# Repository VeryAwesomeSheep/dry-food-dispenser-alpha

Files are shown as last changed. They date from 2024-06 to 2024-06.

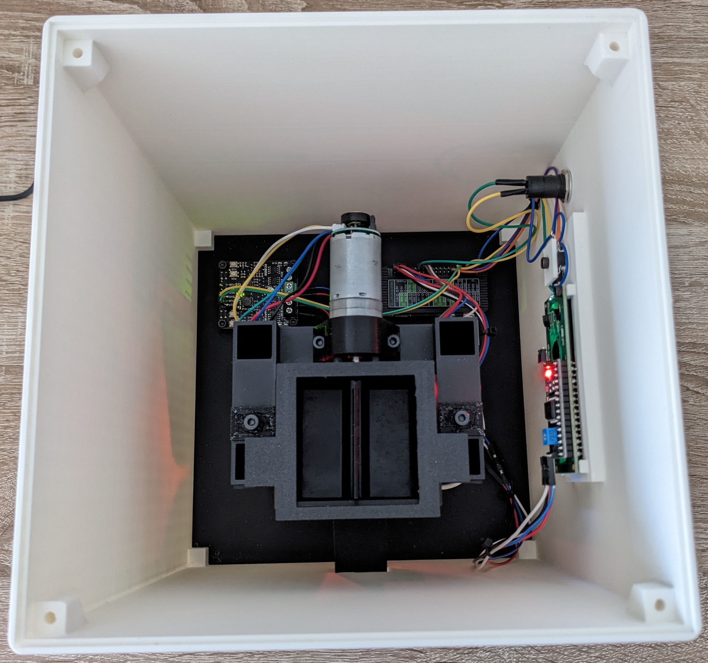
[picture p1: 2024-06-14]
Models/Pictures/inside.jpg

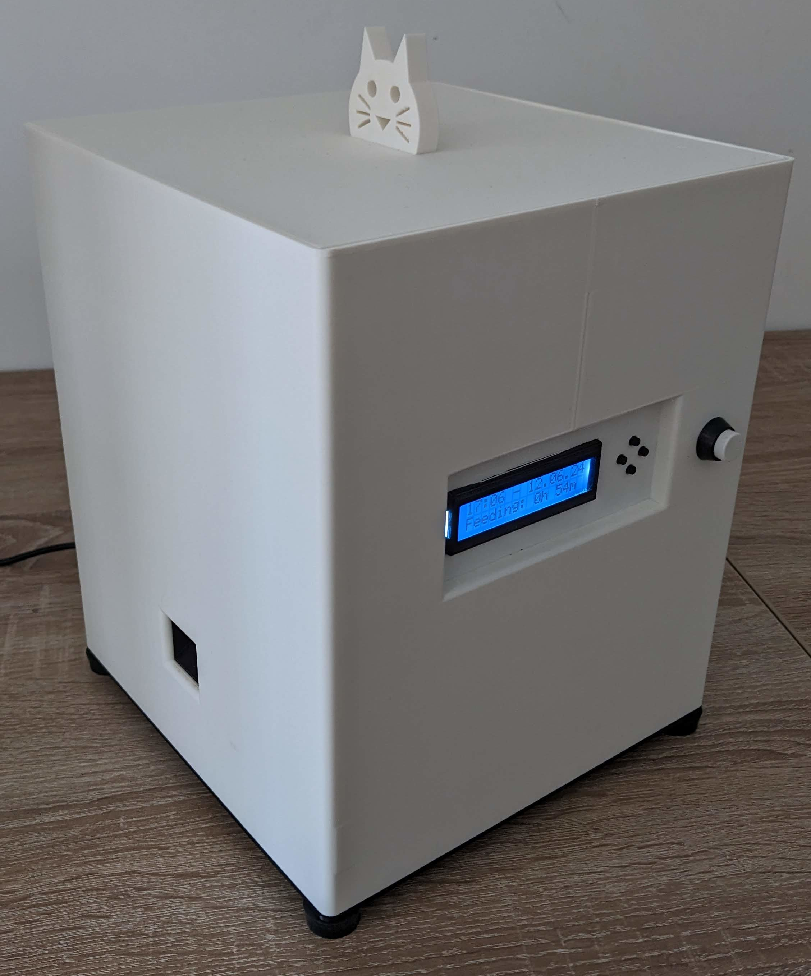
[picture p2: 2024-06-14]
Models/Pictures/front.jpg

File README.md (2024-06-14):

# dry-food-dispenser-alpha
Dry food dispenser for small pets. This was the project for my bachelor thesis. It's an alpha version that I plan on redesigning from the ground up in my spare time as I have some new, possibly better, ideas. All files are here, but I don't recommend building this version yourself.<br>

Project is based on Raspberry Pi Zero 2 W and is powered by a brushed DC motor. Communicaton with user is done via a simple 16x2 LCD display and 5 buttons in a pretty intuitive way. In 99% of cases button up is to go up or increase the value, button down is to go down or decrease the value, button left is to go back or cancel and button right is to go in or confirm. The fifth button called "feed" is used to give the pet a treat and can release a single portion of food when pressed by the user.<br>

Funcionalities of the system are:
- Dispensing food on schedule, fully configured by the user including the time of the day and the amount of portions of food. Limited to 10 feeding times per day, as it seemed more than enough, but it can be adjusted in the code if needed.
- Dispensing food on demand, by pressing the "feed" button.
- Configuring the amount of food per portion, by changing the feeding wheel and then setting the currently used wheel in the user menu.

<p align="center">
<center><image src="Models/Pictures/front.jpg" height="400"></center>
</p>

The dispenser is a fully closed system and it doesn't need any app or internet connection to work, but it's advised to connect the RPi to the internet once at boot to get the time and date for correct working of the scheduler.<br>

Whole system is written in C and it's GPIO functionality relies on [WiringPi](https://github.com/WiringPi/WiringPi) library. Just like the physical design, the code is also planned to be improved, especially the LCD handler as it's hard to read at times and some fragmentation is needed.<br>

The dispenser is powered by a 5V 4A power supply and the motor is controlled by Cytron MDD3A driver which is powered via step-up converter that bumps up the voltage to 6V for the motor. The motor is a 6V LP with 75:1 gearbox with and encoder providing 0.67Nm of torque.<br>

<p align="center">
<image src="Models/Pictures/schematic.png" height="550"></center>
</p>

All other parts are 3D printed and the idea behind them is to be easily mountable and demountable to allow for easy cleaning.

### BOM list
- 1x Raspberry Pi Zero 2 W
- 1x Cytron MDD3A motor driver
- 1x Pololu 2286 motor
- 1x 3-35V to 5-40V 5A step-up converter
- 1x 5V 4A DC power supply
- 1x 16x2 LCD display
- 1x LCD I2C adapter
- 4x Tact Switch TACT-67N
- 1x 12mm push button
- 1x DC-022b power socket
- 1x USB Micro B cabel
- 0.5mm² and 1.5mm² wires
- PLA filament
- PETG filament
- 12x M3x4 screw
- 3x M3x6 screw
- 6x M4x10 screw (+4 optional)
- 1x WaveShare Raspberry Pi Zero/Zero 2 W Heatsink
- 4x rubber feet

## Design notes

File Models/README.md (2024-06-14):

# Real life photos
### Front:
<center><image src="Pictures/front.jpg" height="400"></center>

### Back:
<center><image src="Pictures/back.jpg" height="400"></center>

### Inside:
<center><image src="Pictures/inside.jpg" height="400"></center>

### Inside with food compartment inserted:
<center><image src="Pictures/insideWithFoodCompartment.jpg" height="400"></center>

<br>

# Models:
### Base plate:
<center><image src="Pictures/base.jpg" height="400"></center>

### Cover:
<center><image src="Pictures/cover.jpg" height="400"></center>

### Top cap:
<center><image src="Pictures/topCap.jpg" height="200"></center>

### Food compartment:
<center><image src="Pictures/foodCompartment.jpg" height="400"></center>

### Feeding wheel:
<center><image src="Pictures/millWheel.jpg" height="400"></center>

### Feeding whele cover:
<center><image src="Pictures/wheelCover.jpg" height="400"></center>

### Feeding wheel cover plate:
<center><image src="Pictures/wheelCoverPlate.jpg" height="400"></center>

### Motor holder:
<center><image src="Pictures/motorHolderWithMotor.jpg" height="200"></center>

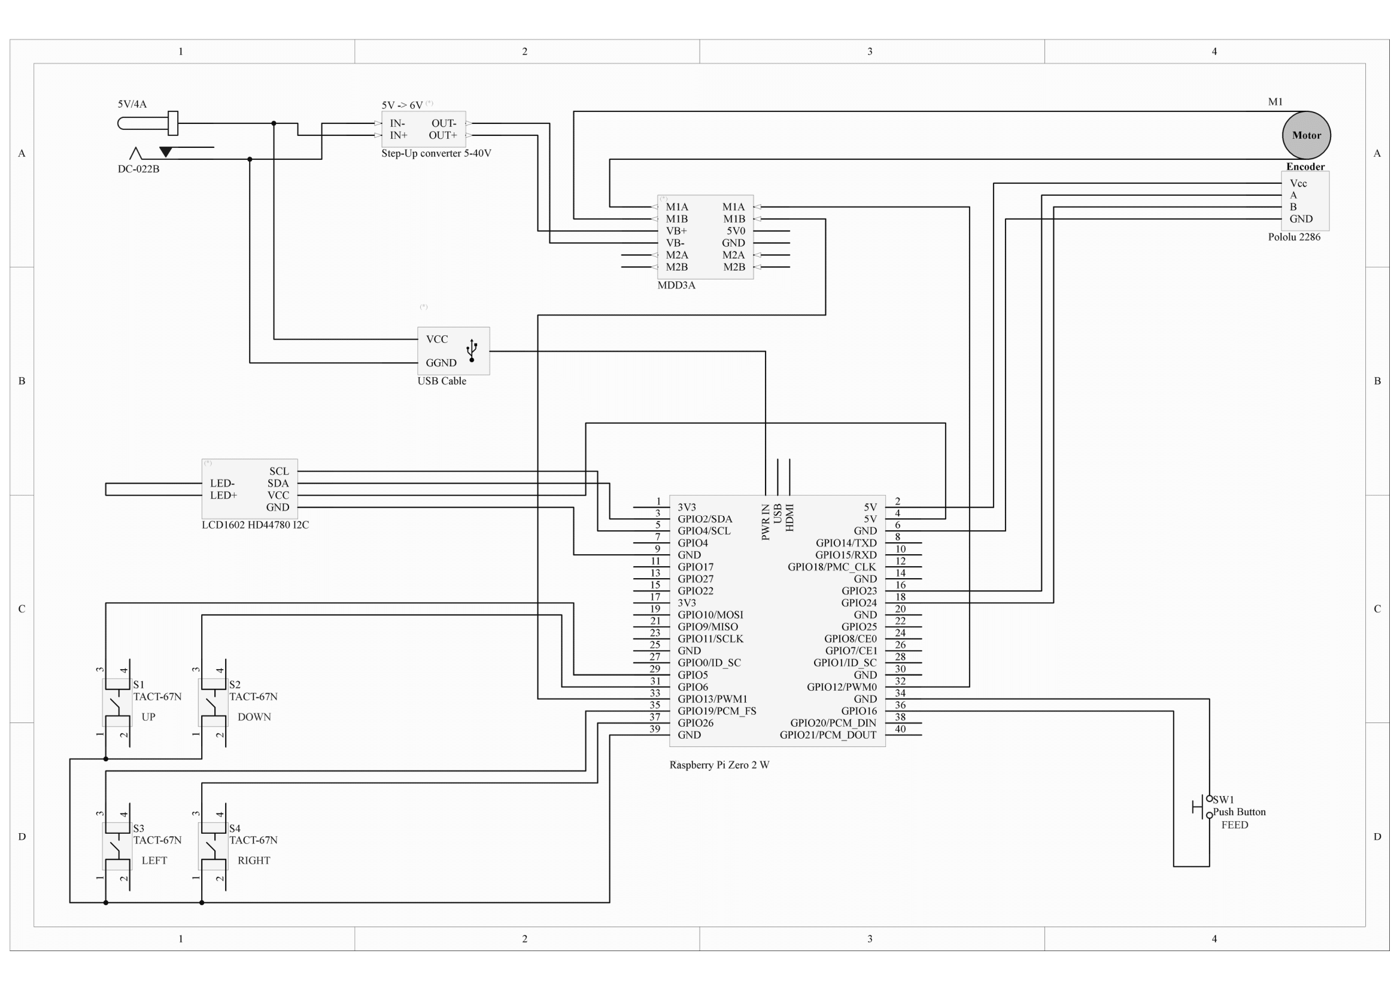
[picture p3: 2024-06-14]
Models/Pictures/schematic.png

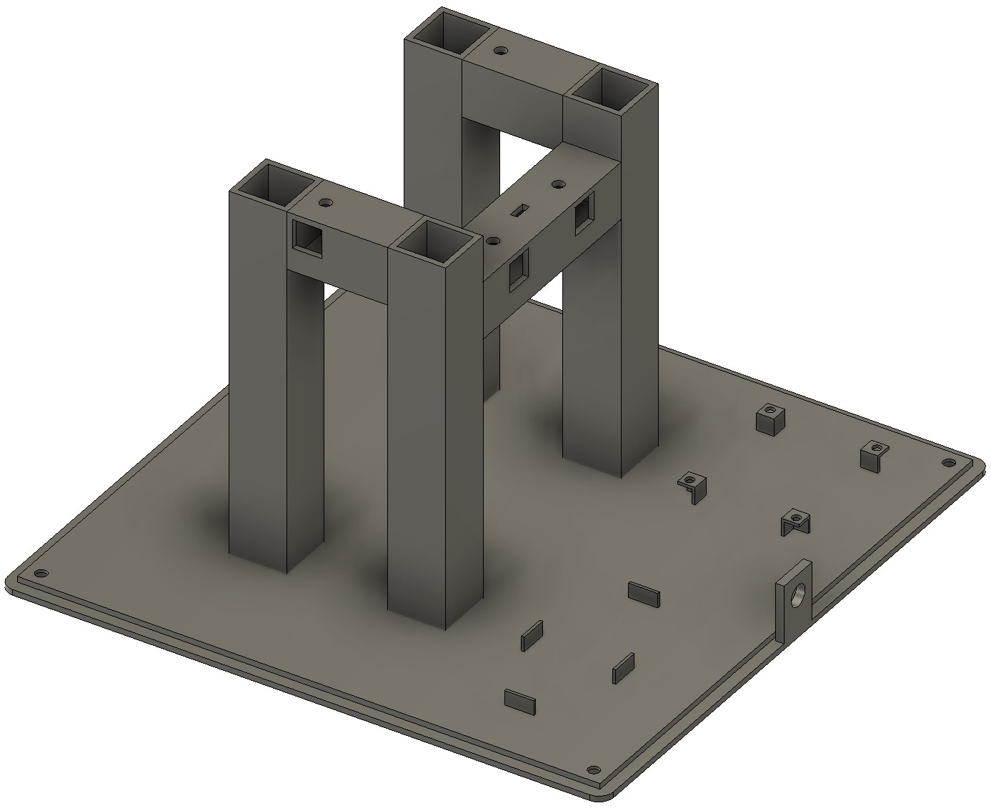
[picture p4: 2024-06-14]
Models/Pictures/base.jpg

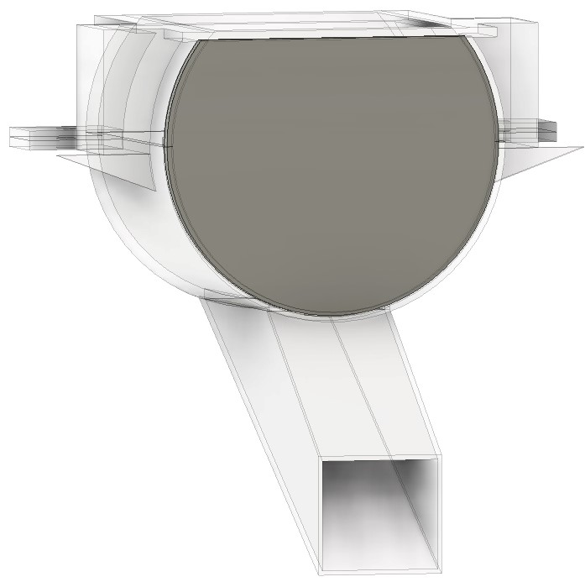
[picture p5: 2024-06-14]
Models/Pictures/wheelCoverPlate.jpg

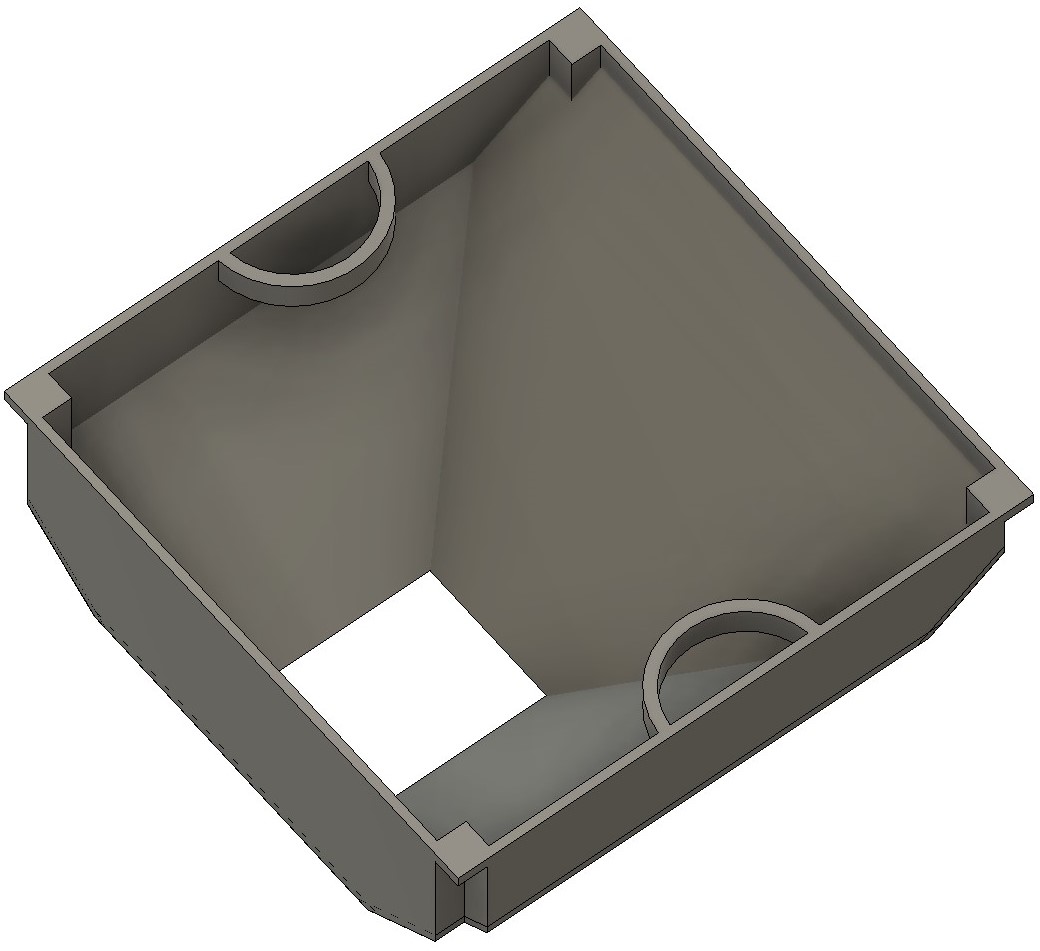
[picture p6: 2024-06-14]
Models/Pictures/foodCompartment.jpg

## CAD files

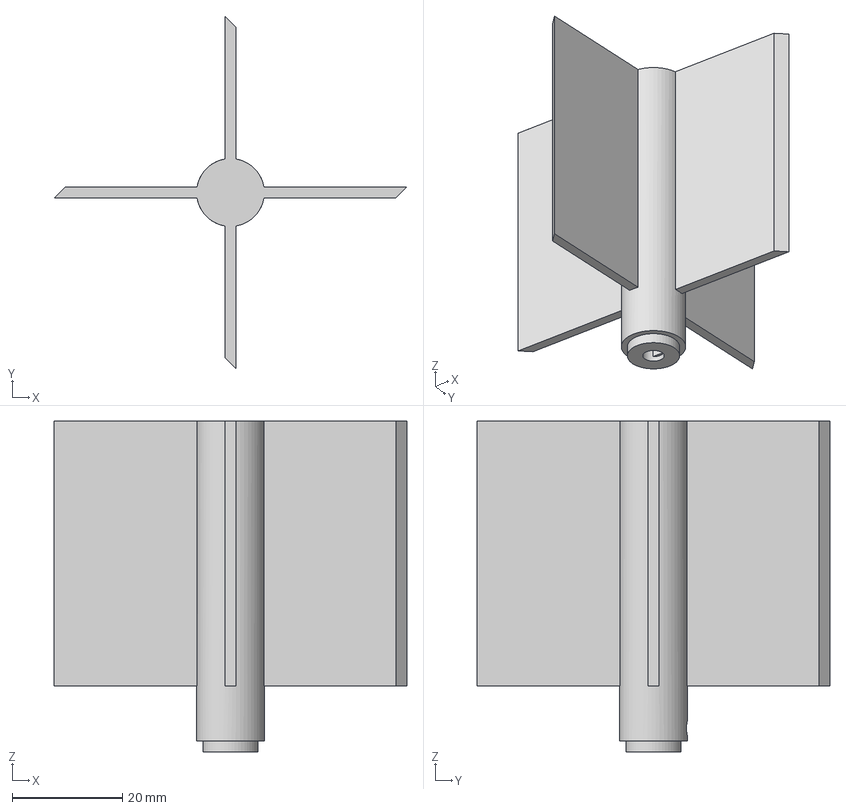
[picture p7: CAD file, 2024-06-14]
Models/Parts/MillWheel.step
64.0 x 64.0 x 60.0 mm

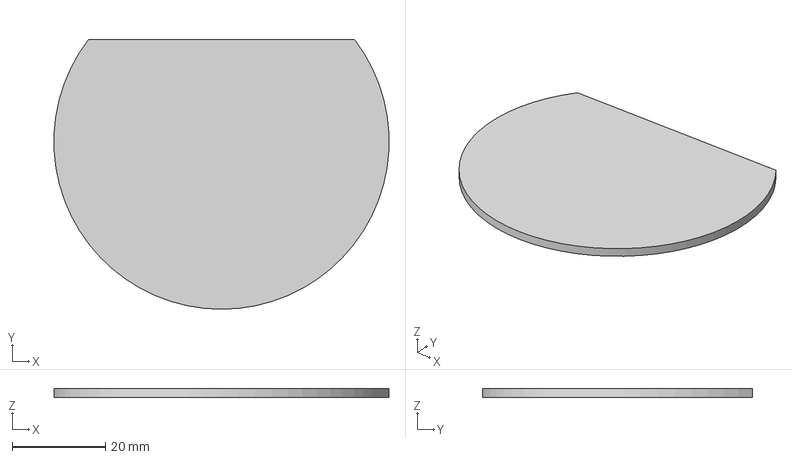
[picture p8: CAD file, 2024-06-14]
Models/Parts/MillWheelClosingPlate.step
71.7 x 57.7 x 2.00 mm

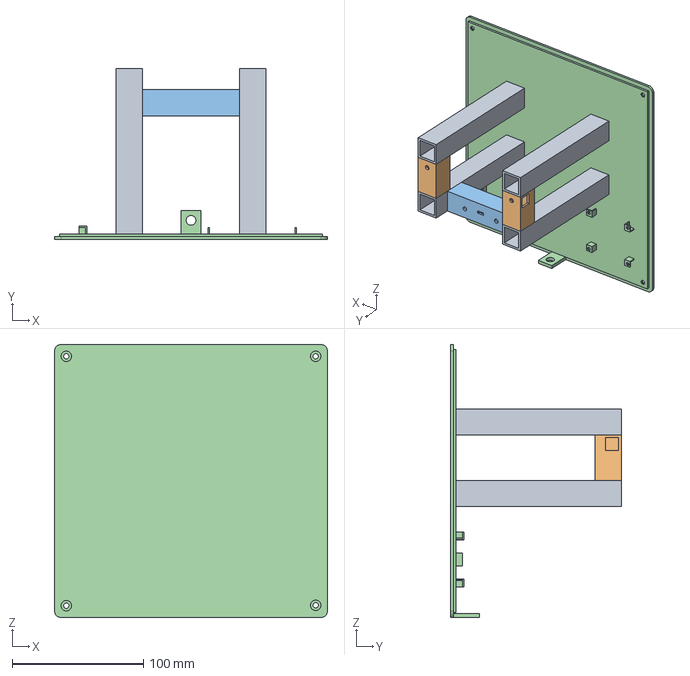
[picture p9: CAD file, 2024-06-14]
Models/Parts/BasePlate.step
208.0 x 130.0 x 208.0 mm

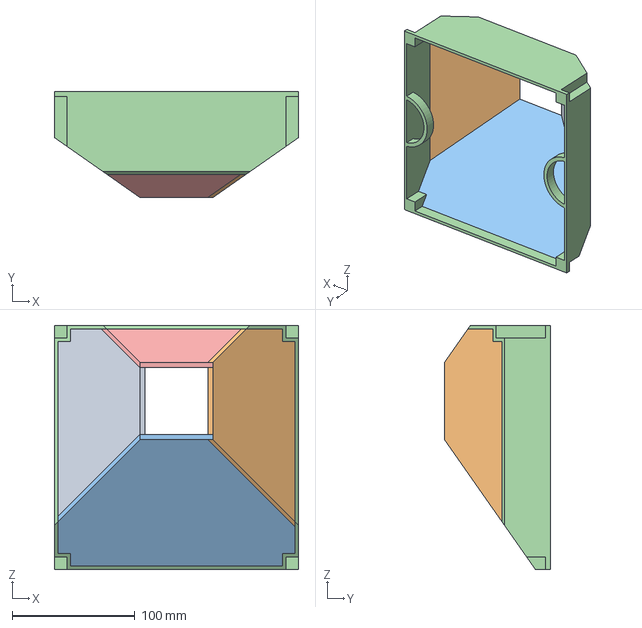
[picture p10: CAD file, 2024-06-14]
Models/Parts/FoodCompartment.step
198.5 x 86.2 x 198.5 mm

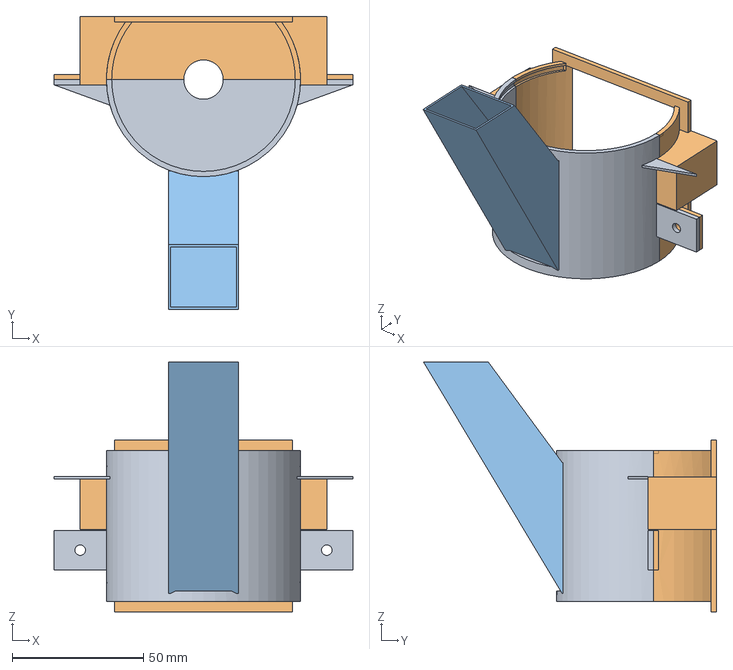
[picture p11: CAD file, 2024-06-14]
Models/Parts/MillWheelCover.step
114.0 x 111.6 x 95.1 mm

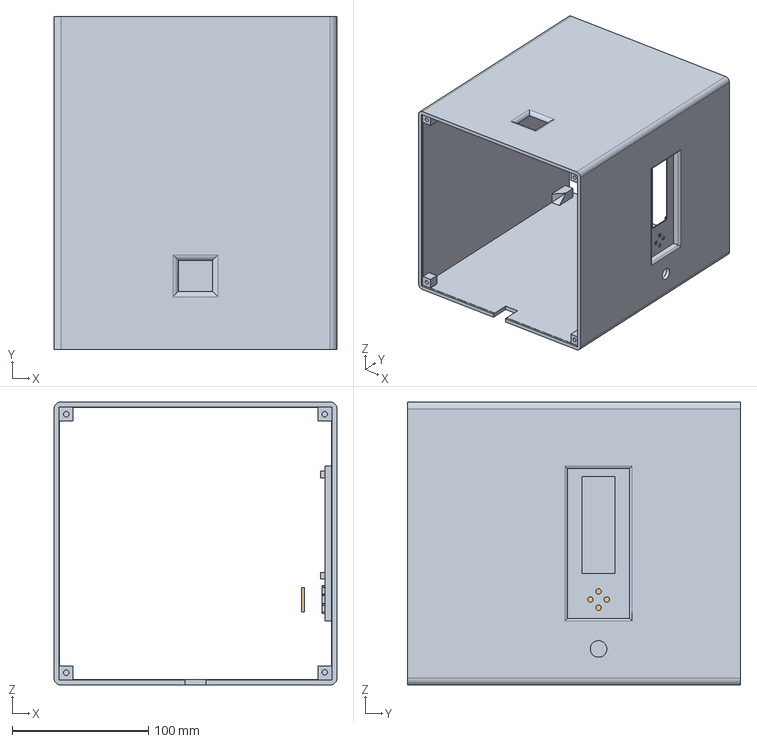
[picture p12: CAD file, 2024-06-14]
Models/Parts/Cover.step
208.0 x 245.0 x 208.0 mm

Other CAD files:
Models/DryFoodDispenser.f3z

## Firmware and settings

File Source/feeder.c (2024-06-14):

// TODO: Clean up includes
#include <stdio.h>
#include <stdint.h>
#include <stdbool.h>
#include <wiringPi.h>
#include "config.h"
#include "libs/tools.h"
#include "libs/lcd.h" // TODO: replace with dynamic library
#include "libs/buttons.h"
#include "libs/motor.h"
#include "libs/lcd_utils.h"
#include "libs/logger.h"
#include "libs/feeding.h"

int main(void) {
  // Initialize logger
  if (initLogger() != 0) {
    fprintf(stderr, "Error during logger initialization: %s", strerror(errno));
    return 1;
  }

  char logMessageBuffer[120];

  // Initialize wiringPi
  if (wiringPiSetupGpio() != 0) {
    sprintf(logMessageBuffer, "Error during wiringPi initialization: %s", strerror(errno));
    logMessage(ERROR, logMessageBuffer);
  }

  // Initialize GPIO pins/devices
  lcd_init_i2c(LCD_ADDRESS, 16, 2, LCD_5x8DOTS);
  lcd_blinkOff_i2c();
  lcd_cursorOff_i2c();

  // Initialize motor
  if (initMotor() != 0) {
    sprintf(logMessageBuffer, "Error during motor initialization: %s", strerror(errno));
    logMessage(ERROR, logMessageBuffer);
    return 1;
  }

  // Initialize buttons
  if (initButtons() != 0) {
    sprintf(logMessageBuffer, "Error during buttons initialization: %s", strerror(errno));
    logMessage(ERROR, logMessageBuffer);
    return 1;
  }

  // Load feeding schedule
  if (loadFeedingSchedule() != 0) {
    sprintf(logMessageBuffer, "No feeding schedule loaded: %s", strerror(errno));
    logMessage(WARNING, logMessageBuffer);
  }

  // Feeder initialization complete
  //lcdWelcomeScreen();
  sprintf(logMessageBuffer, "Feeder initialization complete");
  logMessage(INFO, logMessageBuffer);

  // Operation loop
  while(1) {
    debounceButtons();
    handleFeeding();
    handleLCD();
    delayMicroseconds(10000);
  }

  return 0;
}

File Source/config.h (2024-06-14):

#ifndef config_h
#define config_h

/* LCD Display */
#define LCD_ADDRESS 0x27

/* Buttons */
#define BUTTON_UP 5
#define BUTTON_DOWN 6
#define BUTTON_LEFT 19
#define BUTTON_RIGHT 26
#define BUTTON_FEED 16
#define DEBOUNCE_TIME 20

/* DC Motor */
#define MOTOR_ENCODER_A 23
#define MOTOR_ENCODER_B 24
#define MOTOR_M1A 12
#define MOTOR_M1B 13
#define MOTOR_GEAR_RATIO 74.83
#define MOTOR_CPR 48
#define MOTOR_ENCODER_TICKS_PER_DEGREE (MOTOR_CPR * MOTOR_GEAR_RATIO / 360)

#endif // config_h
